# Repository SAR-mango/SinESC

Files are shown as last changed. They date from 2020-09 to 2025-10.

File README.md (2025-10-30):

# Current State of the Project
This project will be revived when I graduate from UCSB. The following changes are planned:

- Switch to HDI PCB
- Switch to discrete half-bridge gate drivers
- Switch to a variant of the STM32G4 MCU (or whatever seems most appropriate)
- Switch to modern MOSFETs with low gate charge, unchanged 40V Vds, similar Rdson, and high avalanche energy rating
- Simplify current sensing topology
- Implement my own FOC algorithm

These changes mostly improve simplicity and robustness, and will make it easier to develop a 4-in-1 version of SinESC after the single version is fully complete. Currently, SinESC successfully spins motors with 90% efficiency, but there are reliability concerns with the TMC6100 gate driver. Also, some software work is required to add DSHOT support. Finally, a more long-term goal is to develop a self-tuning application integrated with Betaflight that can be run to optimize SinESC for a specific motor.

# Overview
SinESC (pronounced "sign ESC," namesake being the sine wave) is an electronic speed controller (ESC) that supports full sinusoidal control of three-phase brushless DC motors used by RC drone pilots. For a brief visual overview of the project and the underlying theory, see [this presentation](https://github.com/SAR-mango/SinESC/blob/master/sinesc_slides/sinesc_slides.pdf) – adapted from a presentation I gave at SpaceX for an onsite interview.

The real-life dimensions of the PCBs pictured below are 15x30mm.
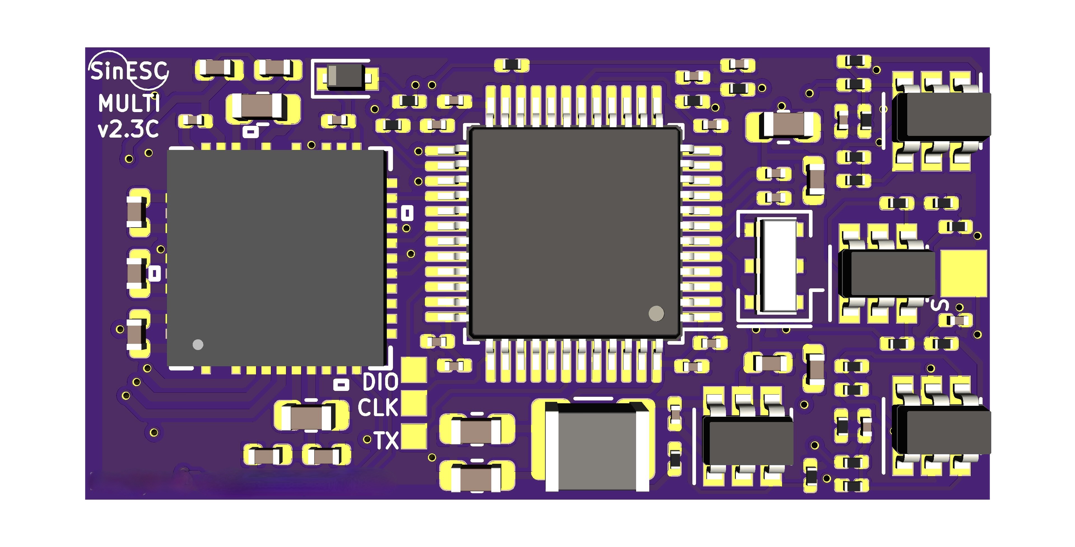
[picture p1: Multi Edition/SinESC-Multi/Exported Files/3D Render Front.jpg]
Multi Edition v2.3C Top

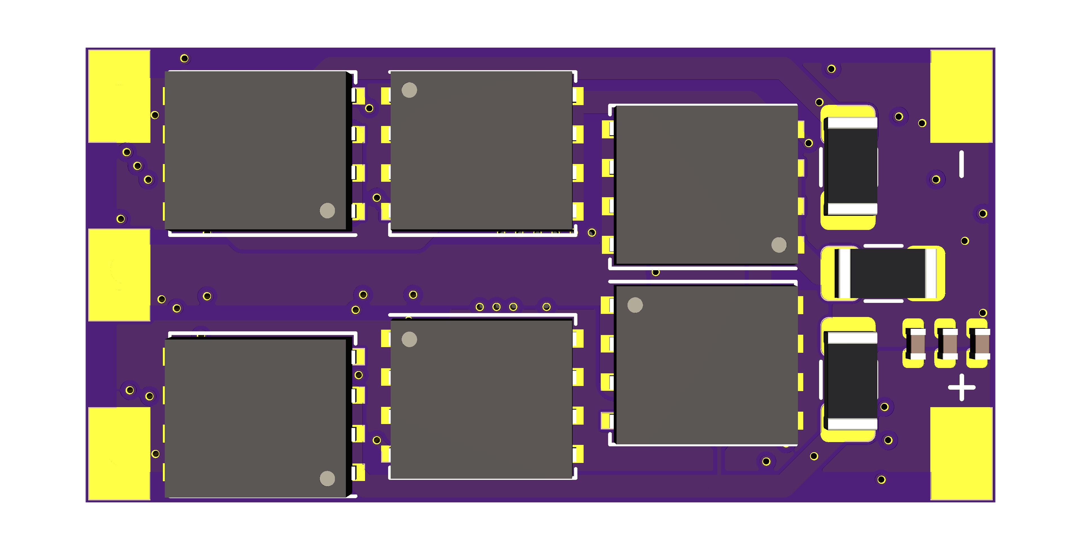
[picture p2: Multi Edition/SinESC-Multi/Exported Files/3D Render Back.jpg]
Multi Edition v2.3C Bottom


# Features, Specifications*
- 90% efficiency (up to 40% longer flight)
- Smooth flight
- Quiet operation
- Bus voltage monitoring for power measurement and under-voltage protection
- Broken-out and labeled debug pins for hackers
- 3–6S Li-po battery support
- Maximum 30A continuous, 40A burst current draw
  - With the greatly-increased efficiency of SinESC, peak motor currents will be significantly lower than before (at a given throttle/thrust level). This does NOT mean your motors produce less power—they are just more efficient.
  - Over-current protection takes advantage of comparators embedded in the microcontroller and triggers immediately at 55A.

\*Several of the above specifications are currently only theoretical; they have not been confirmed with measurements. This page will be updated immediately when any specification changes or is confirmed.

# Sinusoidal Control: Benefits and a Brief Description
Brushless DC motors work best when their phase voltage waveforms are sinusoid-shaped. Try it yourself—connect a BLDC motor to an oscilloscope and spin the rotor with your fingers. You will see a sine wave. 

Regular BLHELI_32 ESCs use a simple "six-point" motor control method in which the phases are energized to bring the rotor to one of six points on a circle. This method is easy to implement as the rotor position at each point will result in a zero-crossing in the back-EMF from the non-energized phase(s), which is easy to detect. This means that the phase voltage waveforms are trapezoid-shaped rather than sinusoid-shaped. This is not ideal as the fields are not *always* aligned with the rotor to maximize torque. This causes the rotor to effectively "jolt in a circle" rather than spin continuously, resulting in lower efficiency and rougher flight. Furthermore, the sharp edges of the trapezoidal signal also introduce high-frequency noise which contributes to the above disadvantages as well. This also makes the motors run louder and hotter.

Sinusoidal control minimizes torque ripple, maximizing efficiency. The magnetic fields are precisely aligned to exert maximum torque on the rotor at *any* given position and power. Minimized torque ripple leads to smoother flight. Greater efficiency (SinESC achieves > 90% efficiency; trapezoidal ESCs typically achieve around 70%) allows for longer flight times and lower peak currents, which can increase battery longevity as well.

# Current-Sense Topology
Not just any ESC can perform sinusoidal control, and not all sinusoidal ESCs are created equal. Sinusoidal control requires that the ESC know the exact position of the rotor in order to properly align the magnetic field. Perfect alignment results in a perfect sine wave.

There are a few ways to find the position of the rotor:
- The first, most obvious method is to put a hall-effect (or similar) sensor on the motor to determine exactly where the rotor is. This sensor simply feeds data to the ESC. However, this is impractical for drones and wings due to durability, size, and weight concerns.
- The second way is to calculate the position of the rotor based on the currents flowing through each phase. Technically, measuring just the total motor current is sufficient, but this leads to poor position estimation and thus reduced performance. Alternatively, each half-bridge can connect to ground through a series current shunt and the voltage drop across each shunt can be amplified and read by an ADC in a microcontroller. This allows for the current through each phase to be known, resulting in far superior performance. Though more complicated, this is the current-sensing topology that SinESC employs.
- Finally, inline current-sensing is also possible. This technique involves placing shunts in series with only two of the three motor phases, since the third phase current can be calculated with Kirchoff's Current Law. However, this requires complicated, expensive amplifiers as high common-mode rejection ratio is critical. Some gate driver ICs integrate these amplifiers, but their gain and offset cannot be tuned to take full advantage of the ADC resolution. At high currents, ADC resolution is very valuable and should not be wasted. Thus, the second method was selected.

# Hardware Achievements
The 15x30mm SinESC Multi Edition PCB uses 0201-sized components when possible for reduced parasitic influences and reduced size. Maximum component density is approximately 50 components/cm². The microcontroller, gate driver, and current-sense amplifiers (all the control electronics) are implemented on the top layer, leaving the bottom layer for the power electronics. This provides room for wide traces. Multi Edition is designed in KiCAD and adheres to OSHPark design rules. All additional libraries are within the project files.

SinESC is designed specifically for efficiency and robustness:
- ST Microelectronics STM32F303C(Bx/Cx) microcontroller
- Maxim Integrated MAX4239 precision op-amps for current-sensing. Incredibly low input offset voltage of 0.1µV. Gain = 30V/V; offset tuned to use the full ADC resolution.
- Low-resistance current shunts (1mΩ) for reduced power loss
- Switching regulator provides logic-level voltage supply for control electronics (efficiency > 80%)
- Thermally optimized PCB layout
- Trinamic Motion Control TMC6100-LA gate driver
  - Fast switching slopes achieved with high gate drive current of 1.5A, decreasing switching losses
- Infineon Technologies BSC010N04LSI N-channel MOSFETs
  - Extremely low on-resistance (Rdson = 1.05mΩ) for reduced power loss
  - High drain-source voltage (Vds = 40V) for immunity to voltage spikes even at 6S Li-po voltages
- High-quality passive components
  - TDK ceramic capacitors
  - Panasonic metal film resistors (all 1% tolerance including shunts)

\*Many of these specifications will change; see the top of this page

# Versions
Regular Semantic Versioning is used for all software components of the project. As for PCB designs, Semantic Versioning has been modified. After Multi v2.3C, versions only reflect the PCB design since schematic changes directly influence the PCB. They are written like so:

vX.YZ where X and Y are numbers and Z is a letter. "v" is sometimes omitted.
- If a minor change is made that does NOT require a new stencil OR an updated BOM, Z is incremented.
- If a minor change requires a new stencil and/or an updated BOM, Y is incremented and Z is reset. Ideally, few minor changes are made between major releases.
- If a major change is made, X is incremented and Y and Z are reset.

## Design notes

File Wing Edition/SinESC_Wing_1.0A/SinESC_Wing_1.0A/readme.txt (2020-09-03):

/**
  * @page Speed regulation using external potentiometer
  * 
  * @verbatim
  ******************** (C) COPYRIGHT 2019 STMicroelectronics *******************
  * @file    STEVAL-ESC001V1\Demonstration\ElectronicSpeedControl\ElectronicSpeedControl.stmcx
  * @author  Motor Control SDK Team
  * @brief   STM32F303 Electronic Speed Control board with BullRunning motor example.
  ******************************************************************************
  * This notice applies to any and all portions of this file
  * that are not between comment pairs USER CODE BEGIN and
  * USER CODE END. Other portions of this file, whether 
  * inserted by the user or by software development tools
  * are owned by their respective copyright owners.
  *
  * Copyright (c) 2019 STMicroelectronics International N.V. 
  * All rights reserved.
  *
  * Redistribution and use in source and binary forms, with or without 
  * modification, are permitted, provided that the following conditions are met:
  *
  * 1. Redistribution of source code must retain the above copyright notice, 
  *    this list of conditions and the following disclaimer.
  * 2. Redistributions in binary form must reproduce the above copyright notice,
  *    this list of conditions and the following disclaimer in the documentation
  *    and/or other materials provided with the distribution.
  * 3. Neither the name of STMicroelectronics nor the names of other 
  *    contributors to this software may be used to endorse or promote products 
  *    derived from this software without specific written permission.
  * 4. This software, including modifications and/or derivative works of this 
  *    software, must execute solely and exclusively on microcontroller or
  *    microprocessor devices manufactured by or for STMicroelectronics.
  * 5. Redistribution and use of this software other than as permitted under 
  *    this license is void and will automatically terminate your rights under 
  *    this license. 
  *
  * THIS SOFTWARE IS PROVIDED BY STMICROELECTRONICS AND CONTRIBUTORS "AS IS" 
  * AND ANY EXPRESS, IMPLIED OR STATUTORY WARRANTIES, INCLUDING, BUT NOT 
  * LIMITED TO, THE IMPLIED WARRANTIES OF MERCHANTABILITY, FITNESS FOR A 
  * PARTICULAR PURPOSE AND NON-INFRINGEMENT OF THIRD PARTY INTELLECTUAL PROPERTY
  * RIGHTS ARE DISCLAIMED TO THE FULLEST EXTENT PERMITTED BY LAW. IN NO EVENT 
  * SHALL STMICROELECTRONICS OR CONTRIBUTORS BE LIABLE FOR ANY DIRECT, INDIRECT,
  * INCIDENTAL, SPECIAL, EXEMPLARY, OR CONSEQUENTIAL DAMAGES (INCLUDING, BUT NOT
  * LIMITED TO, PROCUREMENT OF SUBSTITUTE GOODS OR SERVICES; LOSS OF USE, DATA, 
  * OR PROFITS; OR BUSINESS INTERRUPTION) HOWEVER CAUSED AND ON ANY THEORY OF 
  * LIABILITY, WHETHER IN CONTRACT, STRICT LIABILITY, OR TORT (INCLUDING 
  * NEGLIGENCE OR OTHERWISE) ARISING IN ANY WAY OUT OF THE USE OF THIS SOFTWARE,
  * EVEN IF ADVISED OF THE POSSIBILITY OF SUCH DAMAGE.
  *
  ******************************************************************************
  * @endverbatim
  *
  * @par Demonstration description 
  * 
  *  This demonstration presents motor control application running on 
  * an STEVAL-ESC001V1 electronic speed control board with a BullRunning Motor. 
  *
  * The application features a PWM input for speed reference setting.
  *
  * @par Directory contents 
  * 
  * STEVAL-ESC001V1/Demonstration/ElectronicSpeedControl/readme.txt
  * STEVAL-ESC001V1/Demonstration/ElectronicSpeedControl/ElectronicSpeedControl.ioc
  * STEVAL-ESC001V1/Demonstration/ElectronicSpeedControl/ElectronicSpeedControl.stmcx
  * STEVAL-ESC001V1/Demonstration/ElectronicSpeedControl/Src/esc.c
  * STEVAL-ESC001V1/Demonstration/ElectronicSpeedControl/Src/main.c
  * STEVAL-ESC001V1/Demonstration/ElectronicSpeedControl/Src/mc_config.c
  * STEVAL-ESC001V1/Demonstration/ElectronicSpeedControl/Src/mc_parameters.c
  * STEVAL-ESC001V1/Demonstration/ElectronicSpeedControl/Inc/esc.h
  * STEVAL-ESC001V1/Demonstration/ElectronicSpeedControl/Inc/mc_config.h
  * STEVAL-ESC001V1/Demonstration/ElectronicSpeedControl/Inc/mc_parameters.h
  * STEVAL-ESC001V1/Demonstration/ElectronicSpeedControl/Inc/parameters_conversion_f30x.h
  *
  * @par Hardware and Software environment 
  * 
  * This demonstration runs on the following Hardware Setup:
  * [STEVAL-ESC001V1] + [BullRunning BR2804-1700Kv-1] 
  *
  * The following software tools are needed to run the application:
  *
  * - ST Motor Control SDK, version 5.4.0 or later
  * - STM32CubeMx, version 5.2.0 or later
  * - STM32Cube FW Package for STM32F3 Series, version 1.10.0 or later
  * - IAR EWARM or Keil uVision 5.
  *
  * Note that the current version of this example does not work with STM32CubeIDE 1.0.0.
  *
  * @par How to build it ? 
  * 
  * In order to build the demonstration program, the following is to be done:
  *
  * 1. Open the ElectronicSpeedControl.stmcx file with the STM32 Motor Control Workbench PC software 
  *    tool and save it to another, empty, location.
  *    BEWARE: Do not change the name of the ElectronicSpeedControl.stmcx file, otherwise the example 
  *    will not work properly;
  * 2. Click the Tool -> Generation menu item. This opens a dialog window that lets the users choose
  *    various parameters. Select version 5.2.0 or later for STM32CubeMx, IAR EWARM or Keil MDK Arm 
  *    for the Target toolchain and STM32 FW V1.10.0 or later for the Firmware Package version. Make 
  *    sure to check the HAL - Hardware Abstraction Layer box for the Drive Type. Then, click on the
  *    UPDATE button.
  * 3. Open the generated project with the target IDE;
  * 4. Build the project and load the resulting binary image into your MCU board;
  * 5. Reset your MCU board;
  * 6. Run the example. 
  * 
  * ******************** (C) COPYRIGHT 2019 STMicroelectronics *******************
  **/

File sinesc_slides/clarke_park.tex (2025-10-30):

\begin{tikzpicture}[scale=0.525, every node/.style={transform shape}, >=Latex]
	% --- knobs ---
	\def\R{2}        % circle radius (cm)
	\def\W{3.2}      % waveform width
	\def\A{0.45}     % waveform amplitude
	\def\wfpadT{2} % padding above top circles
	\def\wfpadB{2} % padding below bottom circles
	
	% --- styles ---
	\tikzset{
		circ/.style = {draw, circle, minimum size=2*\R cm},
		axis/.style = {-Latex},
		vec/.style  = {-Latex},
		lbl/.style  = {font=\small}
	}
	
	% --- layout anchors ---
	\coordinate (T1) at (0,5.5);
	\coordinate (T2) at (6.6,5.5);
	\coordinate (T3) at (13.2,5.5);
	\coordinate (B1) at (0,0);
	\coordinate (B2) at (6.6,0);
	\coordinate (B3) at (13.2,0);
	
	% ================== TOP ROW — VOLTAGE ==================
	\node[circ] (C_T1) at (T1) {};
	\draw[axis] (C_T1.center) -- ++(0,\R) node[lbl,above] {$U_D$};
	\draw[axis] (C_T1.center) -- ++(\R,0) node[lbl,right] {$U_Q$};
	\node[align=center, lbl, above=10pt of C_T1] {Rotational steady-state \\ output currents};
	
	\node[circ] (C_T2) at (T2) {};
	\draw[axis] (C_T2.center) -- ++(0,\R) node[lbl,above] {$U_\beta$};
	\draw[axis] (C_T2.center) -- ++(\R,0) node[lbl,right] {$U_\alpha$};
	\node[align=center, lbl, above=10pt of C_T2] {Orthogonal output currents};
	
	\node[circ] (C_T3) at (T3) {};
	\foreach \ang/\name/\pos in {90/U_V/above, -30/U_U/right, -150/U_W/left}{
		\draw[vec] (C_T3.center) -- ++(\ang:\R);
		\node[lbl,\pos] at ($(C_T3.center)+(\ang:\R)$) {$\name$};
	}
	\node[align=center, lbl, above=10pt of C_T3] {Three-phase output waveform};
	
	% arrows across the top row
	\draw[-Latex] ($(C_T1.east)+(0.6,0)$) -- node[above=6pt,lbl]{iPARK}    ($(C_T2.west)+(-0.6,0)$);
	\draw[-Latex] ($(C_T2.east)+(0.6,0)$) -- node[above=6pt,lbl]{iCLARKE} ($(C_T3.west)+(-0.6,0)$);
	\draw[-Latex] ($(C_T3.east)+(0.6,0)$) -- node[above=6pt,lbl]{SVPWM} ($(C_T3.east)+(0.6,0)+(C_T3.west)+(-0.6,0)-(C_T2.east)-(0.6,0)$);
	
	% ================== BOTTOM ROW — CURRENT ==================
	\node[circ] (C_B1) at (B1) {};
	\draw[axis] (C_B1.center) -- ++(0,\R) node[lbl,above] {$I_D$};
	\draw[axis] (C_B1.center) -- ++(\R,0) node[lbl,right] {$I_Q$};
	\node[align=center, lbl, below=6pt of C_B1] {Rotational steady-state \\ direct and quadrature currents};
	
	\node[circ] (C_B2) at (B2) {};
	\draw[axis] (C_B2.center) -- ++(0,\R) node[lbl,above] {$I_\beta$};
	\draw[axis] (C_B2.center) -- ++(\R,0) node[lbl,right] {$I_\alpha$};
	\node[align=center, lbl, below=6pt of C_B2] {Two orthogonal currents};
	
	\node[circ] (C_B3) at (B3) {};
	\foreach \ang/\name/\pos in {90/I_V/above, -30/I_U/right, -150/I_W/left}{
		\draw[vec] (C_B3.center) -- ++(\ang:\R);
		\node[lbl,\pos] at ($(C_B3.center)+(\ang:\R)$) {$\name$};
	}
	\node[align=center, lbl, below=6pt of C_B3] {Three linearly dependent currents};
	
	% arrows across the bottom row
	\draw[-Latex] ($(C_B3.west)+(-0.6,0)$) -- node[above=6pt,lbl]{CLARKE} ($(C_B2.east)+(0.6,0)$);
	\draw[-Latex] ($(C_B2.west)+(-0.6,0)$) -- node[above=6pt,lbl]{PARK}  ($(C_B1.east)+(0.6,0)$);
	\draw[-Latex] ($(C_B1.east)!0.5!(C_B2.west)-(0,1.2)$) node[below=6pt,lbl]{Rotor position $\theta$} -- ($(C_B1.east)!0.5!(C_B2.west)$);
	
	% PID controllers arrow (downward)
	\draw[Latex-]
	($(C_T1.south)+(0,-0.1)$) -- node[lbl,left=3pt,align=center]{PID controller\\$I_{D}=0$\\$I_{Q}\propto\text{torque setpoint}$}
	($(C_B1.north)+(0,0.4)$);
	
	% ================== WAVEFORMS ==================
	% ---- TOP: above circles ----
	\begin{scope}[shift={($(C_T1.center)+(0,\R+\wfpadT)$)}]
		\draw [Red] ({-0.5*\W},0) -- ({0.5*\W},0)
		node[Red,lbl,anchor=west] {$U_Q$};
		\draw [blue] ({-0.5*\W},-\A) -- ({0.5*\W},-\A)
		node[blue,lbl,anchor=west] {$U_D$};
	\end{scope}
	
	\begin{scope}[shift={($(C_T2.center)+(0,\R+\wfpadT)$)}]
		\draw[Red,samples=120,domain=0:360,variable=\t,smooth]
		plot ({-0.5*\W + \W*\t/360},{ \A*sin(\t)}) node[Red,lbl,anchor=west] at ({0.5*\W},{0}) {$U_\alpha$};
		\draw[blue,samples=120,domain=0:360,variable=\t,smooth]
		plot ({-0.5*\W + \W*\t/360},{ \A*sin(\t-90)}) node[blue,lbl,anchor=west] at ({0.5*\W},{-\A}) {$U_\beta$};
	\end{scope}
	
	\begin{scope}[shift={($(C_T3.center)+(0,\R+\wfpadT)$)}]
		\draw[Red,samples=120,domain=0:360,variable=\t,smooth]
		plot ({-0.5*\W + \W*\t/360},{ \A*sin(\t)}) node[Red,lbl,anchor=west] at ({0.5*\W},{0}) {$U_U$};
		\draw[Green,samples=120,domain=0:360,variable=\t,smooth]
		plot ({-0.5*\W + \W*\t/360},{ \A*sin(\t-120)}) node[Green,lbl,anchor=west] at ({0.5*\W},{-\A}) {$U_V$};
		\draw[blue,samples=120,domain=0:360,variable=\t,smooth]
		plot ({-0.5*\W + \W*\t/360},{ \A*sin(\t+120)}) node[blue,lbl,anchor=west] at ({0.5*\W},{\A}) {$U_W$};
	\end{scope}
	
	% ---- BOTTOM: below circles ----
	\begin{scope}[shift={($(C_B1.center)+(0,-\R-\wfpadB)$)}]
		\draw [Red] ({-0.5*\W},0) -- ({0.5*\W},0)
		node[Red,lbl,anchor=west] {$I_Q$};
		\draw [blue] ({-0.5*\W},-\A) -- ({0.5*\W},-\A)
		node[Blue,lbl,anchor=west] {$I_D$};
	\end{scope}
	
	\begin{scope}[shift={($(C_B2.center)+(0,-\R-\wfpadB)$)}]
		\draw[Red,samples=120,domain=0:360,variable=\t,smooth]
		plot ({-0.5*\W + \W*\t/360},{ \A*sin(\t)}) node[Red,lbl,anchor=west] at ({0.5*\W},{0}) {$I_\alpha$};
		\draw[blue,samples=120,domain=0:360,variable=\t,smooth]
		plot ({-0.5*\W + \W*\t/360},{ \A*sin(\t-90)});
		\node[blue,lbl,anchor=west] at ({0.5*\W},{-\A}) {$I_\beta$};
	\end{scope}
	
	\begin{scope}[shift={($(C_B3.center)+(0,-\R-\wfpadB)$)}]
		\draw[Red,samples=120,domain=0:360,variable=\t,smooth]
		plot ({-0.5*\W + \W*\t/360},{ \A*sin(\t)}) node[Red,lbl,anchor=west] at ({0.5*\W},{0}) {$I_U$};
		\draw[Green,samples=120,domain=0:360,variable=\t,smooth]
		plot ({-0.5*\W + \W*\t/360},{ \A*sin(\t-120)}) node[Green,lbl,anchor=west] at ({0.5*\W},{-\A}) {$I_V$};
		\draw[blue,samples=120,domain=0:360,variable=\t,smooth]
		plot ({-0.5*\W + \W*\t/360},{ \A*sin(\t+120)});
		\node[blue,lbl,anchor=west] at ({0.5*\W},{\A}) {$I_W$};
	\end{scope}
\end{tikzpicture}

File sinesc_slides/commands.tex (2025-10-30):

\let\union\cup
\let\intersect\cap
\let\w\omega
\let\e\epsilon
\let\ve\varepsilon
\let\prefto\succ
\let\nprefto\prec
\let\ans\tcboxmath

\let\Re\relax
\DeclareMathOperator{\Re}{Re}
\let\Im\relax
\DeclareMathOperator{\Im}{Im}
\DeclareMathOperator{\Nul}{Nul}
\DeclareMathOperator{\Col}{Col}
\DeclareMathOperator{\Row}{Row}
\DeclareMathOperator{\Span}{Span}
\DeclareMathOperator{\tr}{tr}
\DeclareMathOperator{\rref}{rref}

\newcommand{\V}[1]{V_{\text{#1}}}
\newcommand{\VR}[1]{V_{R_{\text{#1}}}}
\newcommand{\VL}[1]{V_{L_{\text{#1}}}}
\newcommand{\VC}[1]{V_{C_{\text{#1}}}}
\newcommand{\Vv}[1]{v_{\text{#1}}}

\newcommand{\I}[1]{I_{\text{#1}}}
\newcommand{\IR}[1]{I_{R_{\text{#1}}}}
\newcommand{\IL}[1]{I_{L_{\text{#1}}}}
\newcommand{\IC}[1]{I_{C_{\text{#1}}}}
\newcommand{\Ii}[1]{i_{\text{#1}}}

\renewcommand{\P}[1]{P_{\text{#1}}}
\newcommand{\PR}[1]{P_{R_{\text{#1}}}}
\newcommand{\PL}[1]{P_{L_{\text{#1}}}}
\newcommand{\PC}[1]{P_{C_{\text{#1}}}}

\newcommand{\U}[1]{U_{\text{#1}}}
\newcommand{\E}[1]{E_{\text{#1}}}

\newcommand{\A}[1]{A_{\text{#1}}}

\newcommand{\Z}[1]{Z_{\text{#1}}}
\newcommand{\R}[1]{R_{\text{#1}}}
\newcommand{\Rr}[1]{r_{\text{#1}}}
\newcommand{\C}[1]{C_{\text{#1}}}
\newcommand{\Ll}[1]{L_{\text{#1}}}

\newcommand{\qv}[1]{\qty{#1}{\volt}}
\newcommand{\qkv}[1]{\qty{#1}{\kilo\volt}}
\newcommand{\qmv}[1]{\qty{#1}{\milli\volt}}
\newcommand{\quv}[1]{\qty{#1}{\micro\volt}}
\newcommand{\qnv}[1]{\qty{#1}{\nano\volt}}
\newcommand{\qMv}[1]{\qty{#1}{\mega\volt}}

\newcommand{\qa}[1]{\qty{#1}{\ampere}}
\newcommand{\qma}[1]{\qty{#1}{\milli\ampere}}
\newcommand{\qua}[1]{\qty{#1}{\micro\ampere}}
\newcommand{\qna}[1]{\qty{#1}{\nano\ampere}}

\newcommand{\qw}[1]{\qty{#1}{\watt}}
\newcommand{\qkw}[1]{\qty{#1}{\kilo\watt}}
\newcommand{\qmw}[1]{\qty{#1}{\milli\watt}}
\newcommand{\quw}[1]{\qty{#1}{\micro\watt}}
\newcommand{\qnw}[1]{\qty{#1}{\nano\watt}}
\newcommand{\qMw}[1]{\qty{#1}{\mega\watt}}

\newcommand{\qj}[1]{\qty{#1}{\joule}}
\newcommand{\qkj}[1]{\qty{#1}{\kilo\joule}}
\newcommand{\qmj}[1]{\qty{#1}{\milli\joule}}
\newcommand{\quj}[1]{\qty{#1}{\micro\joule}}
\newcommand{\qnj}[1]{\qty{#1}{\nano\joule}}
\newcommand{\qMj}[1]{\qty{#1}{\mega\joule}}

\newcommand{\qr}[1]{\qty{#1}{\ohm}}
\newcommand{\qkr}[1]{\qty{#1}{\kilo\ohm}}
\newcommand{\qmr}[1]{\qty{#1}{\milli\ohm}}
\newcommand{\qur}[1]{\qty{#1}{\micro\ohm}}
\newcommand{\qnr}[1]{\qty{#1}{\nano\ohm}}
\newcommand{\qMr}[1]{\qty{#1}{\mega\ohm}}

\newcommand{\qf}[1]{\qty{#1}{\farad}}
\newcommand{\qmf}[1]{\qty{#1}{\milli\farad}}
\newcommand{\quf}[1]{\qty{#1}{\micro\farad}}
\newcommand{\qnf}[1]{\qty{#1}{\nano\farad}}
\newcommand{\qpf}[1]{\qty{#1}{\pico\farad}}

\newcommand{\qh}[1]{\qty{#1}{\henry}}
\newcommand{\qmh}[1]{\qty{#1}{\milli\henry}}
\newcommand{\quh}[1]{\qty{#1}{\micro\henry}}
\newcommand{\qnh}[1]{\qty{#1}{\nano\henry}}

\newcommand{\qhz}[1]{\qty{#1}{\hertz}}
\newcommand{\qkhz}[1]{\qty{#1}{\kilo\hertz}}
\newcommand{\qMhz}[1]{\qty{#1}{\mega\hertz}}
\newcommand{\qGhz}[1]{\qty{#1}{\giga\hertz}}
\newcommand{\qThz}[1]{\qty{#1}{\tera\hertz}}

\newcommand{\qkm}[1]{\qty{#1}{\kilo\meter}}
\newcommand{\qm}[1]{\qty{#1}{\meter}}
\newcommand{\qcm}[1]{\qty{#1}{\centi\meter}}
\newcommand{\qmm}[1]{\qty{#1}{\milli\meter}}
\newcommand{\qum}[1]{\qty{#1}{\micro\meter}}
\newcommand{\qnm}[1]{\qty{#1}{\nano\meter}}
\newcommand{\qpm}[1]{\qty{#1}{\pico\meter}}

\newcommand{\qkg}[1]{\qty{#1}{\kilo\gram}}
\newcommand{\qg}[1]{\qty{#1}{\gram}}
\newcommand{\qmg}[1]{\qty{#1}{\milli\gram}}
\newcommand{\qug}[1]{\qty{#1}{\micro\gram}}

\newcommand{\qs}[1]{\qty{#1}{\second}}
\newcommand{\qms}[1]{\qty{#1}{\milli\second}}
\newcommand{\qus}[1]{\qty{#1}{\micro\second}}
\newcommand{\qns}[1]{\qty{#1}{\nano\second}}
\newcommand{\qps}[1]{\qty{#1}{\pico\second}}

\newcommand{\qnc}[1]{\qty{#1}{\nano\coulomb}}

\newcommand{\qdb}[1]{\qty{#1}{\decibel}}

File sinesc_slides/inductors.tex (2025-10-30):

\begin{circuitikz}
	\coordinate (C) at (0,0);
	\coordinate (M) at (90:2);
	\coordinate (N) at (-30:2);
	\coordinate (P) at (210:2);
	% Inductors with filled center node and open end nodes
	\draw [L,o-*] (M) to (C);
	\draw (C) to[L,-o] (N);
	\draw [L,o-] (P) to (C);
	% Labels
	\node[above]       at (M) {U};
	\node[below right] at (N) {W};
	\node[below left]  at (P) {V};
\end{circuitikz}

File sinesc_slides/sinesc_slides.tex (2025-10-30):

\input{setup}
\input{commands}
\title{FOC Motor Controller for Drones}
\author{Erk Sampat}
\date{October 3, 2025}
\begin{document}
\begin{frame}
	\begin{center}
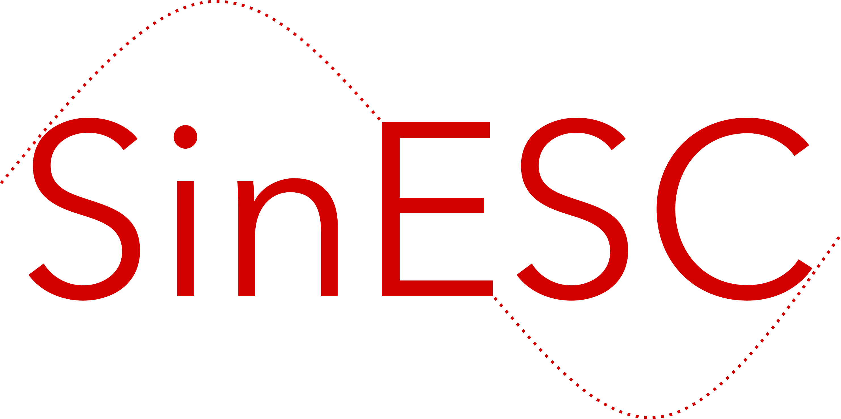
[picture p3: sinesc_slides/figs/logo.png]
		
	\end{center}
	\vskip-0.5in
	\titlepage
\end{frame}
\begin{frame}\frametitle{Outline}
	\begin{enumerate}
		\item Project Introduction
		\item Theory
		\item Design Walkthrough
	\end{enumerate}
\end{frame}
\begin{frame}\frametitle{Project Introduction -- The Problem}
	\begin{itemize}
		\item Typical FPV drone flight time: 5--7 minutes
		\item Off-the-shelf brushless motor controller efficiency $\approx 70\%$
		\item Can we achieve closer to $100\%$?
		\item Yes! With a better control scheme.
		\item Motor controller (``ESC'') is accessible for improvement
	\end{itemize}
	\begin{center}
		
	\end{center}
\end{frame}
\begin{frame}\frametitle{Project Introduction -- System Overview}
	\only<1-2>{
		\begin{center}
			\input{system_diagram}
		\end{center}
	}
	\only<3>{
		\begin{center}
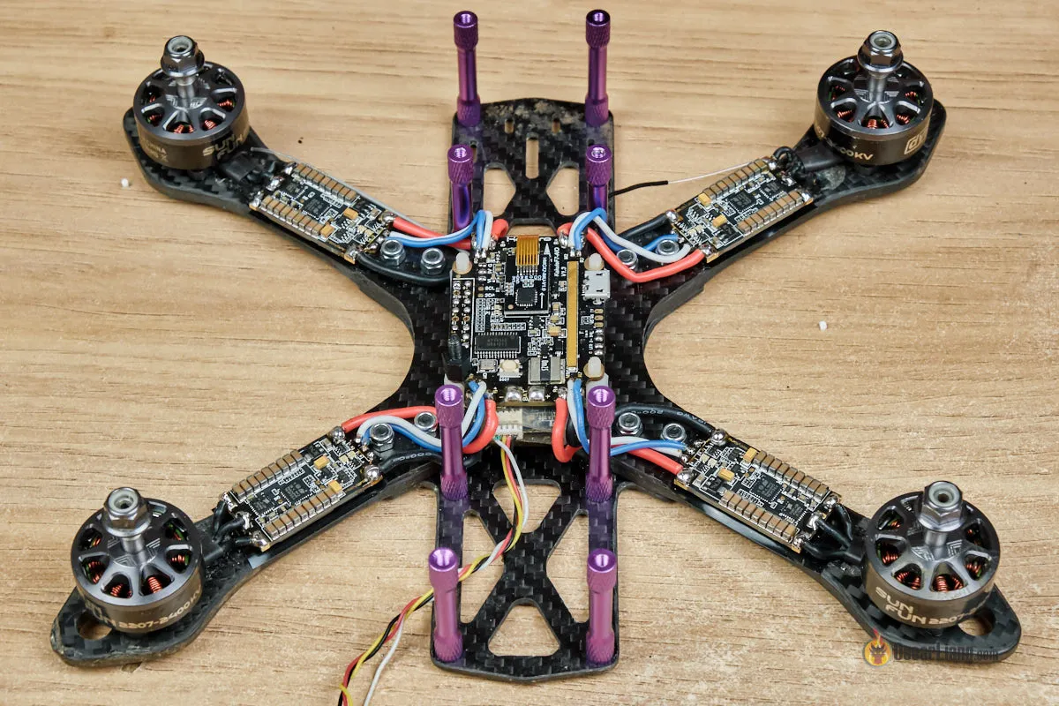
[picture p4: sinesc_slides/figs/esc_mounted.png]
			
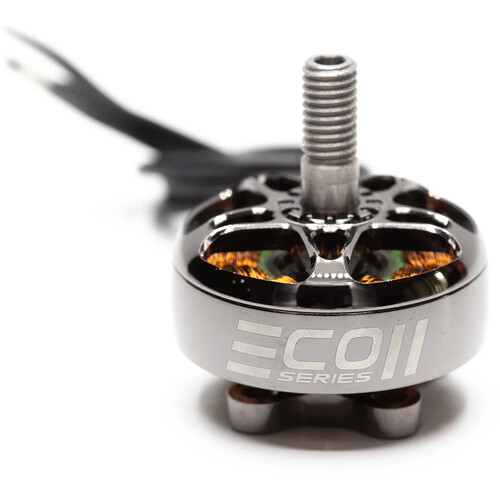
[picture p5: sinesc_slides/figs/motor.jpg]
			
		\end{center}
	}
\end{frame}
\begin{frame}\frametitle{Project Introduction -- Scope}
	\begin{itemize}
		\item Designed/fabricated/tested custom hardware to run sensorless FOC
		\item Hardware initially designed in 2020
		\item Future plan: fully custom firmware
	\end{itemize}
	\begin{center}
		\only<1>{}
		\only<2>{}
	\end{center}
\end{frame}
\begin{frame}\frametitle{Project Introduction -- Primary Specifications}
	\begin{itemize}
		\item $\V{in}$: \qv{12}--\qv{25.2} (4S--6S Li-po battery)
		\item $\I{in}$: \qa{45} continuous, \qa{55} burst (5 seconds)
		\item DSHOT communication protocol support
		\item Size: comparable to off-the-shelf ESC (\qmm{15}$\times$\qmm{30})
		\item Out-of-box compatibility with broad range of motors
		\item High reliability: robustness against\ldots
		\begin{itemize}
			\item Voltage spikes
			\item Rapid throttle (speed command) changes
			\item Physical shock
		\end{itemize}
	\end{itemize}
\end{frame}
\begin{frame}\frametitle{Theory -- Brushless Motors}
	\begin{minipage}{0.5\textwidth}
		\begin{itemize}
			\item Rotor: permanent magnets
			\item Stator: coil windings
			\item Electronically commutated
			\item PMSM: sinusoidal BEMF
			\item BLDC: trapezoidal BEMF\ldots \\
			but often looks sinusoidal due to LC filtering by windings
		\end{itemize}
	\end{minipage}%
	\begin{minipage}{0.5\textwidth}
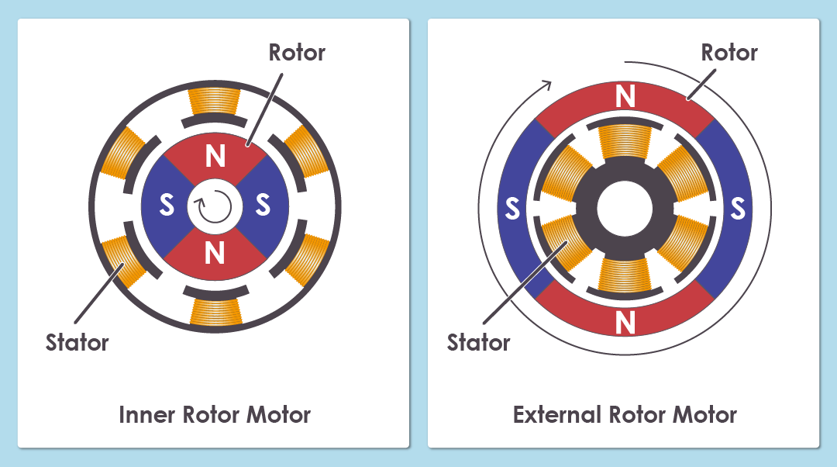
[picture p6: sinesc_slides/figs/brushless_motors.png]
		
		{\scriptsize ablic.com}
		\begin{center}
			\input{inductors}
		\end{center}
	\end{minipage}
\end{frame}
\begin{frame}\frametitle{Theory -- 6-Step Drive}
	\begin{minipage}{0.6\textwidth}
		Operation:
		\begin{itemize}
			\item 6 energized states
			\item Switch upon zero-crossing
			\item PWM controls torque
		\end{itemize}
		Benefits:
		\begin{itemize}
			\item Simple
			\item Low switching loss
			\item Zero-crossings measured on floating phase
		\end{itemize}
		Drawbacks:
		\begin{itemize}
			\item Torque ripple
			\item High-frequency harmonics
			\item Field not always orthogonal to rotor\ldots inefficient
		\end{itemize}
	\end{minipage}%
	\begin{minipage}{0.4\textwidth}
		\begin{center}
			\input{table}
			\input{6_step}
		\end{center}
	\end{minipage}
\end{frame}
\begin{frame}\frametitle{Theory -- Field-Oriented Control}
	\begin{minipage}{0.6\textwidth}
		Operation:
		\begin{itemize}
			\item $\infty$ energized ``states''
			\item Space-vector modulation
			\item PWM controls torque AND field orientation
		\end{itemize}
		Benefits:
		\begin{itemize}
			\item Low torque ripple
			\item Reduced harmonics
			\item Field always orthogonal to rotor\ldots highly efficient
		\end{itemize}
		Drawbacks:
		\begin{itemize}
			\item Complex
			\item Higher switching loss
			\item Difficult to measure BEMF
			\item Requires precise position sensing
		\end{itemize}
	\end{minipage}%
	\begin{minipage}{0.4\textwidth}
		\begin{center}
			\input{table}
			\input{foc}
		\end{center}
	\end{minipage}
\end{frame}
\begin{frame}\frametitle{Theory -- Clarke-Park Transforms}
	\begin{center}
		\input{clarke_park}
	\end{center}
\end{frame}
\begin{frame}\frametitle{Theory -- Sensorless Position Estimation}
	Key point: $\text{knowing BEMF and phase currents}=\text{knowing rotor position}$
	\begin{enumerate}
		\item Measure phase voltage during short non-energized intervals
		\begin{itemize}
			\item High speed required for large BEMF\ldots
			\item but non-energized intervals shorten as speed increases
		\end{itemize}
		\item Estimate BEMF using measured currents and motor parameters $L$ and $R$ per phase
		\item Calculate electrical angle of rotor, differentiate w.r.t. time to obtain speed
		\begin{itemize}
			\item Helps to know rotor inertia
		\end{itemize}
	\end{enumerate}
	More advanced techniques: high-frequency injection, PLL, etc.
\end{frame}
\begin{frame}\frametitle{Design Walkthrough -- Schematic}
	
\end{frame}
\begin{frame}\frametitle{Design Walkthrough -- Key Component Characteristics}
	\begin{minipage}[t]{0.5\textwidth}
		Microcontroller
		\begin{itemize}
			\item ST part -- FOC library
			\item Ample analog peripherals
			\item 32 bit, medium performance
		\end{itemize}
	\end{minipage}%
	\begin{minipage}[t]{0.5\textwidth}
		Current-sense amplifiers
		\begin{itemize}
			\item Low noise
			\item Sufficient bandwidth
			\item Temperature stability
		\end{itemize}
	\end{minipage}
	\vskip 1em
	\begin{minipage}[t]{0.5\textwidth}
		FET driver
		\begin{itemize}
			\item Simplicity
			\item Robustness against transients
			\item Sufficient drive current
			\item High-side N support
		\end{itemize}
	\end{minipage}%
	\begin{minipage}[t]{0.5\textwidth}
		MOSFETs
		\begin{itemize}
			\item $\R{ds,on}$ low enough
			\item $Q_{\text{g}}$ as low as possible
			\item Sufficient $\V{ds}$
			\item N-channel
		\end{itemize}
	\end{minipage}
\end{frame}
\begin{frame}\frametitle{Design Walkthrough -- Component Choices}
	\begin{minipage}[t]{0.5\textwidth}
		Microcontroller: STM32F3xx
		\begin{itemize}
			\item Multiple ADCs
			\item Comparators for OCP
			\item ST FOC library
			\item Cortex-M3
		\end{itemize}
	\end{minipage}%
	\begin{minipage}[t]{0.5\textwidth}
		Current-sense amplifiers: MAX4239
		\begin{itemize}
			\item Somewhat poor choice
			\item \quv{0.1} input offset voltage unnecessary
			\item Too expensive
		\end{itemize}
	\end{minipage}
	\vskip 1em
	\begin{minipage}[t]{0.5\textwidth}
		FET driver: TMC6100
		\begin{itemize}
			\item Expensive and complicated
			\item Charge pump for 100\% duty cycle operation
			\item Controlled through SPI
		\end{itemize}
	\end{minipage}%
	\begin{minipage}[t]{0.5\textwidth}
		MOSFETS: BSC010N04LSI
		\begin{itemize}
			\item $\V{ds}=\qv{40}$
			\item $R_{\text{ds,on}}=\qmr{1.05}$: too low
			\item $Q_{\text{g}}=\qnc{87}$: too high
			\item Ideally, find middle ground by considering product $R_{\text{ds,on}}Q_{\text{g}}$
		\end{itemize}
	\end{minipage}
\end{frame}
\begin{frame}\frametitle{Design Walkthrough -- Challenges}
	\begin{minipage}{0.6\textwidth}
		\begin{itemize}
			\item SPI configuration
			\item Inappropriate current specification
			\item \qv{3.3} rail issue
			\item Gate driver charge pump filter
			\item Form factor; difficulty with testing
			\item ADC resolution for current sensing
		\end{itemize}
	\end{minipage}%
	\begin{minipage}{0.4\textwidth}
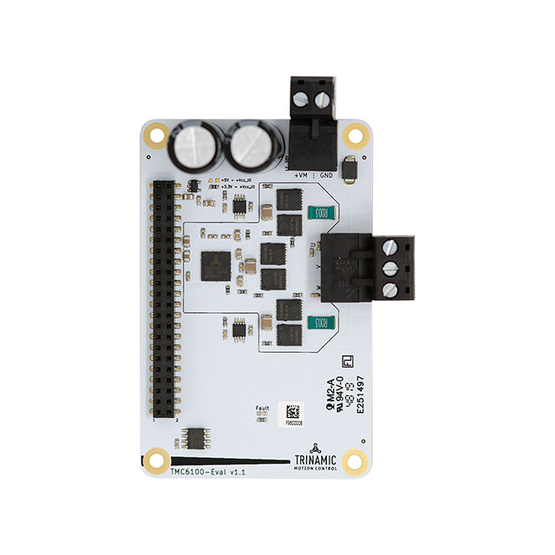
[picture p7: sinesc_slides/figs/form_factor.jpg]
		
	\end{minipage}
	\begin{center}
		
		
	\end{center}
\end{frame}
\begin{frame}\frametitle{Design Walkthrough -- Assembly}
	\begin{itemize}
		\item Initially: stencil, pick \& place, and reflow manually
		\item Later: assembled at PCBWay
	\end{itemize}
	\begin{center}
		
		
	\end{center}
\end{frame}
\end{document}

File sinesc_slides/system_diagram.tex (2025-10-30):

\begin{tikzpicture}[scale=0.9,transform shape]
	% Paths, nodes and wires:
	\node[shape=rectangle, draw, line width=0.5pt, minimum width=5.982cm, minimum height=4.982cm] at (35, -4){};
	\node[shape=rectangle, draw, line width=0.5pt, minimum width=2.232cm, minimum height=0.982cm] at (35, -0.75){} node[anchor=center, align=center, text width=1.862cm, inner sep=5.5pt] at (35, -0.75){Battery};
	\node[shape=rectangle, draw, line width=0.5pt, minimum width=2.232cm, minimum height=0.982cm] at (30.625, -4){} node[anchor=center, align=center, text width=1.862cm, inner sep=5.5pt] at (30.625, -4){RC Receiver};
	\node[shape=rectangle, draw, line width=0.5pt, dash pattern={on 2pt off 1pt}, minimum width=2.482cm, minimum height=0.982cm] at (35, -5.5){} node[anchor=center, align=center, text width=2.112cm, inner sep=5.5pt] at (35, -5.5){IMU};
	\node[shape=rectangle, draw, line width=0.5pt, dash pattern={on 2pt off 1pt}, minimum width=2.482cm, minimum height=0.982cm] at (35, -4){} node[anchor=center, align=center, text width=2.112cm, inner sep=5.5pt] at (35, -4){MCU};
	\node[shape=rectangle, draw, line width=0.5pt, dash pattern={on 2pt off 1pt}, minimum width=2.482cm, minimum height=0.982cm] at (35, -2.5){} node[anchor=center, align=center, text width=2.112cm, inner sep=5.5pt] at (35, -2.5){Power Distribution};
	\path[draw=Red, line width=0.8pt, -latex] (35, -1.25) -- (35, -2);
	\draw[-latex] (31.75, -4) -- (33.75, -4);
	\draw[-latex] (35, -5) -- (35, -4.5);
	\path[draw=Red, line width=0.8pt, -latex] (36.75, -2.5) -- (36.75, -5.5) -- (36.25, -5.5);
	\node[shape=rectangle, minimum width=3.215cm, minimum height=0.965cm] at (33.375, -1.75){} node[anchor=center, align=center, text width=2.827cm, inner sep=6pt] at (33.375, -1.75){Flight Controller};
	\only<1>{\node[shape=rectangle, draw, line width=0.5pt, minimum width=2.215cm, minimum height=0.965cm] at (39.375, -4){} node[anchor=center, align=center, text width=1.827cm, inner sep=6pt] at (39.375, -4){4x ESC};}
	\only<2>{\node[shape=rectangle, draw=blue, line width=1pt, minimum width=2.215cm, minimum height=0.965cm] at (39.375, -4){} node[anchor=center, align=center, text width=1.827cm, inner sep=6pt] at (39.375, -4){4x ESC};}
	\node[shape=rectangle, draw, line width=0.5pt, minimum width=2.232cm, minimum height=0.982cm] at (39.375, -5.5){} node[anchor=center, align=center, text width=1.862cm, inner sep=5.5pt] at (39.375, -5.5){4x Motor};
	\path[draw=Red, line width=0.8pt, -latex] (36.75, -4.25) -- (36.25, -4.25);
	\draw[-latex] (35, -3) -- (35, -3.5);
	\path[draw=Red, line width=0.8pt, latex-] (30.625, -3.5) |- (30.75, -2.5) -- (33.75, -2.5);
	\path[draw=Red, line width=0.8pt, -latex] (36.25, -2.5) -| (39.375, -3.5);
	\draw[-latex] (36.25, -4) -- (38.25, -4);
	\path[draw=Red, line width=0.8pt, -latex] (39.375, -4.5) -- (39.375, -5);
\end{tikzpicture}

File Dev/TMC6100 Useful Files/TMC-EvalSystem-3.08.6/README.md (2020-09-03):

# TMC-EvalSystem

Trinamic Evaluation System

## Setup
To clone this repository, simply use the following command in order to clone submodules recursively:  
`git clone --recurse-submodules git@github.com:trinamic/TMC-EvalSystem.git`

## Changelog

For detailed changelog, see commit history.

### Version 3.06: (Beta)
* Full TMC2160 support
* Landungsbruecke HW v2.0 support with internal HWID detection for future revisions
* Internal/external step/dir generator handling in FW and IDE
* Various bugfixes
* Internal optimizations

### Version 3.05: (Released)
* TMC5072-EVAL Critical bugfix at register access
* TMC2160-EVAL Corrected pin layout

### Version 3.02: (Released)
* Reworked chip register configuration mechanisms (generic reset/restore procedures implemented in API)
* Changed register accesses to use a unified Mask/Shift macro approach
* Various bugfixes

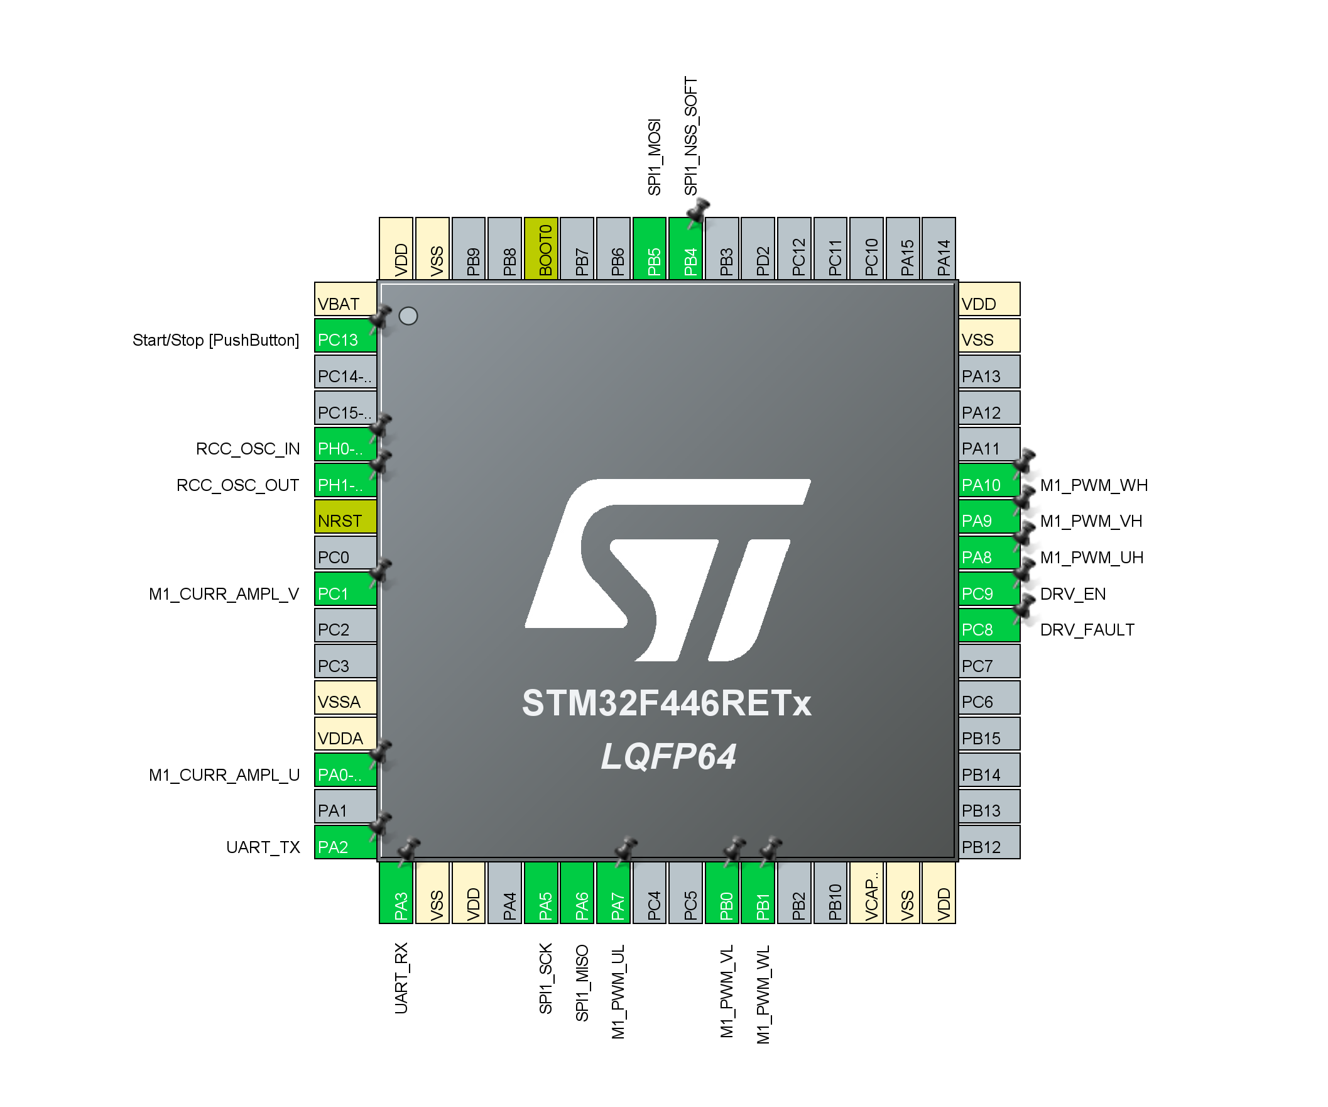
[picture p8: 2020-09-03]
Dev/F446RE_Eval_Test/Pinout.png

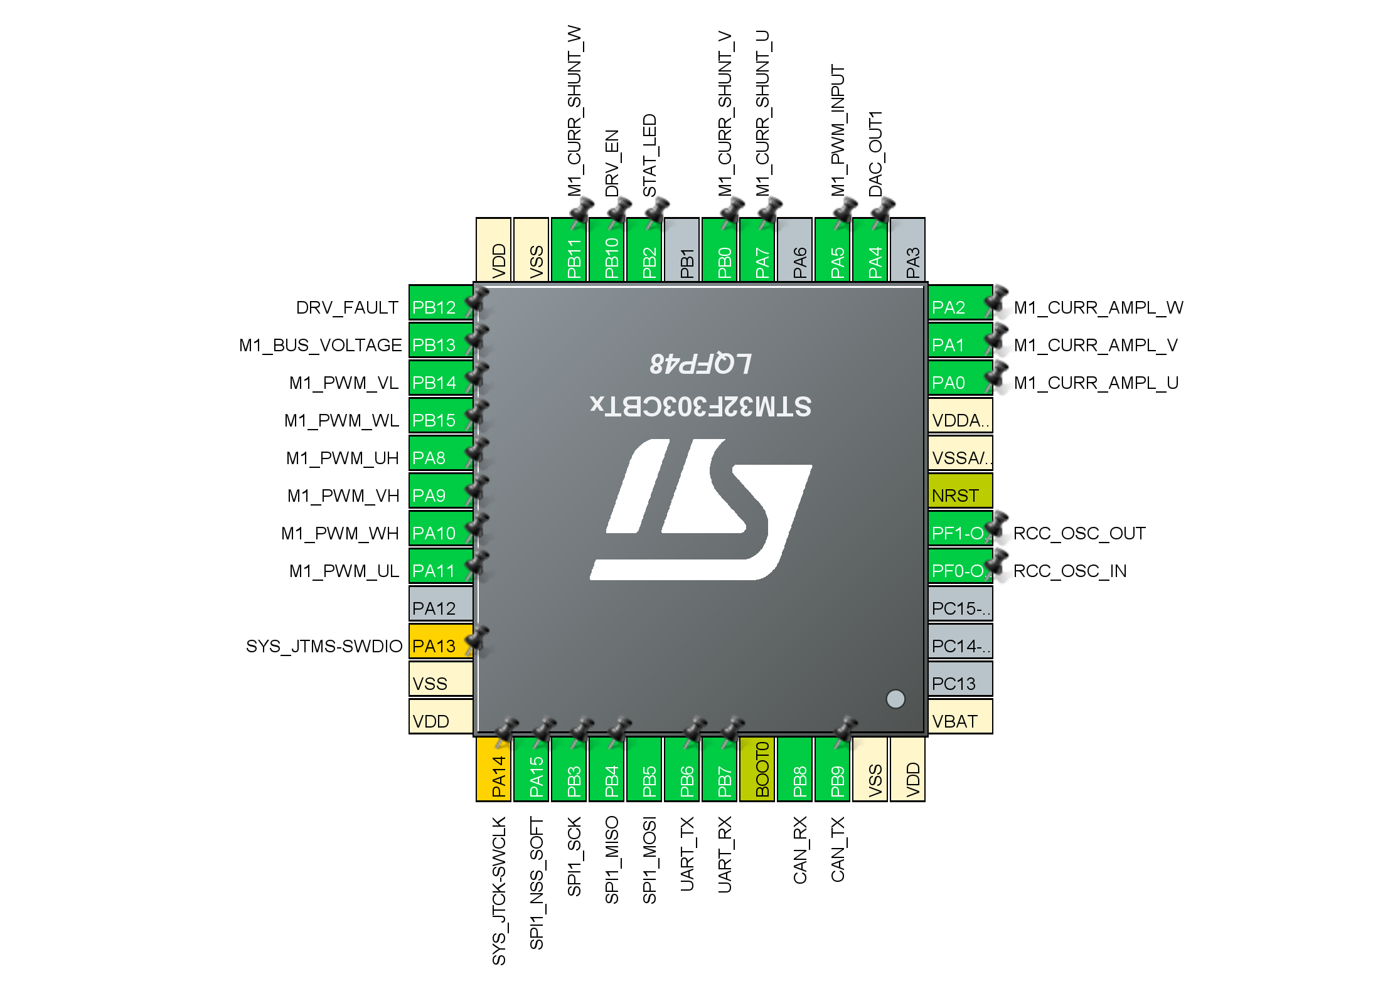
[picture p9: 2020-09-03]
Wing Edition/Pinout.png

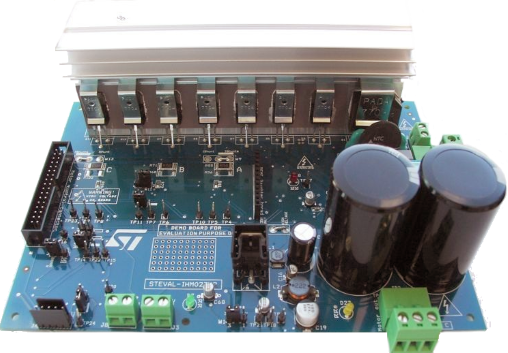
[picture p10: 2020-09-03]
Dev/Original ST Software/STSW-ESC001V1/ESC_STMotorProfiler_addon/resources/assets/images/power/en_steval-ihm023v3.png

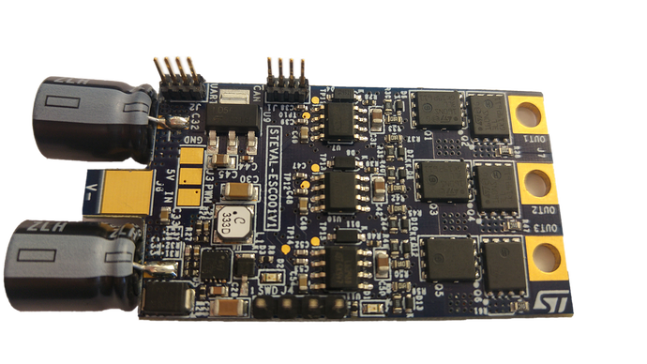
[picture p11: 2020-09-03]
Dev/Original ST Software/STSW-ESC001V1/ESC_STMotorProfiler_addon/resources/assets/boardConfigs/images/STEVAL-ESC001V1_PB.png

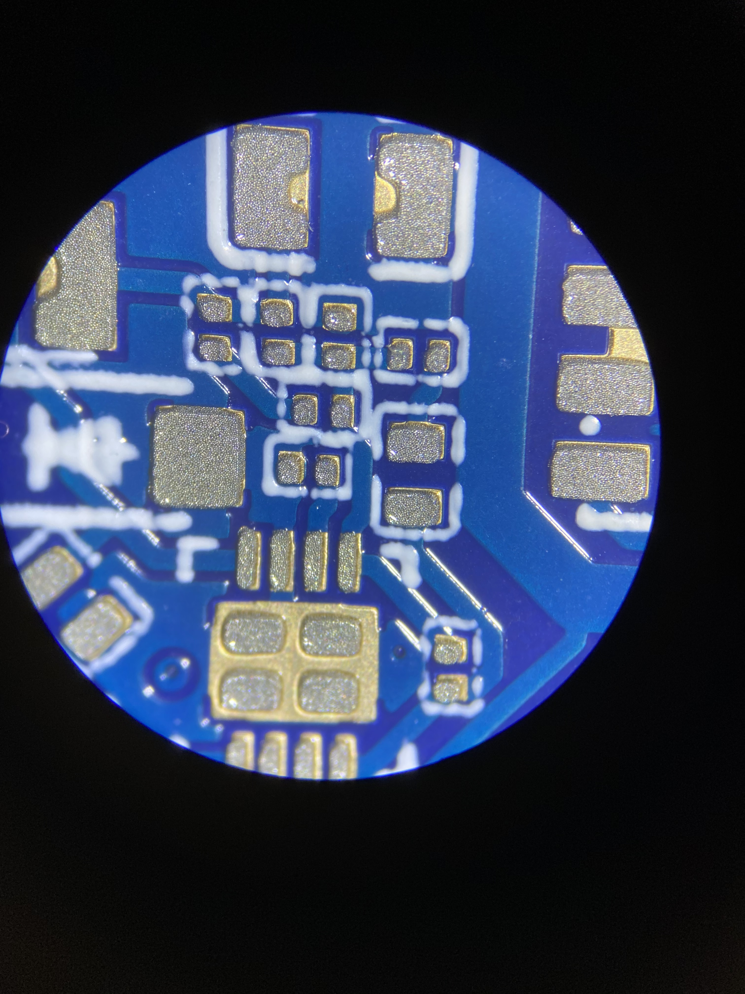
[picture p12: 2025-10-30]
sinesc_slides/figs/stencil_microscope.jpeg

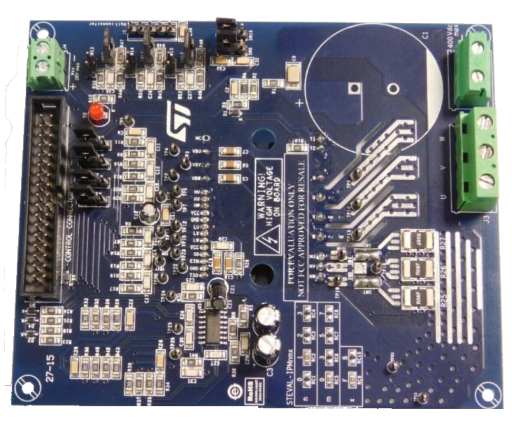
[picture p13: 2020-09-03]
Dev/Original ST Software/STSW-ESC001V1/ESC_STMotorProfiler_addon/resources/assets/images/power/steval-ipm10f.png

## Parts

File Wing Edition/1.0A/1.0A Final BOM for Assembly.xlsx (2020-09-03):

Name | Designator | Footprint | Quantity
8MHz | X1 | - | 1
Red LED | LED1 | LED_0201 | 1
MAX4239AUT+T | U5,U6,U7 | SOT23-6 | 3
SM04B-GHS-TB(LF)(SN)- | J1 | - | 1
BAT30F4 | D1 | D0201 | 1
PMEG4030ER/8X | D2 | SOD-123 | 1
1mΩ | R3,R1,R2 | R1206 | 3
0Ω | R17,R16,R20,R21,R18,R19 | R0201 | 6
680Ω | R28,R24,R34 | R0201 | 3
220Ω | R8 | R0201 | 1
100kΩ | R5 | R0201 | 1
12kΩ | R6 | R0201 | 1
86.6Ω | R10,R25,R31 | R0201 | 3
1.5kΩ | R9 | R0201 | 1
120Ω | R4 | R0201 | 1
249Ω | R11 | R0201 | 1
4.99kΩ | R14 | R0201 | 1
1.1kΩ | R15 | R0201 | 1
220kΩ | R7 | R0201 | 1
976Ω | R13,R27,R33 | R0201 | 3
15kΩ | R22,R29,R35 | R0201 | 3
470Ω | R23,R30,R36 | R0201 | 3
5.1kΩ | R12,R26,R32 | R0201 | 3
6.8nF | C25,C32,C35 | C0201 | 3
100nF | C6,C12,C4,C2,C1,C13,C3 | C0201 | 7
2.2nF | C24 | C0201 | 1
1µF | C10,C28,C29,C30 | C0402 | 4
22µF | C27 | C0805 | 1
10nF | C5 | C0201 | 1
10µF | C14 | C0805 | 1
470nF | C15,C26 | C0402 | 2
4.7µF | C11 | C0603 | 1
1nF | C9,C7,C8 | C0201 | 3
22nF | C19 | C0603 | 1
100nF | C22,C23,C16 | C0402 | 3
15nF | C31,C34,C33 | C0402 | 3
22nF | C20 | C0402 | 1
10µF | C17 | C0603 | 1
2.2µF | C18 | C0402 | 1
470pF | C21 | C0201 | 1
TMC6100-LA | U4 | LQFP37 | 1
TJA1051TK/3,118 | U1 | HVSON-8 | 1
BSC010N04LSI | Q1,Q2,Q3,Q4,Q5,Q6 | PG-TDSON-8-FL | 6
L7981TR | U3 | VFQFPN8 | 1
10µH | L1 | IND-SMD_L2.0-W2.0 | 1
STM32F303CBT7 | U2 | STM-LQFP48 | 1

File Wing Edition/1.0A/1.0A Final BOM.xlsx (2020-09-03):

Index | Quantity | Part Number | Manufacturer Part Number | Description | Customer Reference | Backorder | Unit Price | Extended Price
1 | 1 | SMD4300TF10-ND | SMD4300TF10 | TACK FLUX 10CC WATER WASHABLE |  | 0 | 17.95 | $17.95
2 | 12 | 445-12081-1-ND | CGA1A2X7R1C682K030BA | CAP CER 6800PF 16V X7R 0201 |  | 0 | 0.085 | $1.02
3 | 4 | P122674CT-ND | ERJ-1GNF1101C | RES SMD 1.1K OHM 1% 1/20W 0201 |  | 0 | 0.1 | $0.40
4 | 1 | DS18B20+T&RCT-ND | DS18B20+T&R | SENSOR DIGITAL -55C-125C TO92-3 |  | 0 | 3.92 | $3.92
5 | 4 | P122834CT-ND | ERJ-1GNF2203C | RES SMD 220K OHM 1% 1/20W 0201 |  | 0 | 0.1 | $0.40
6 | 4 | P122864CT-ND | ERJ-1GNF2490C | RES SMD 249 OHM 1% 1/20W 0201 |  | 0 | 0.1 | $0.40
7 | 4 | P122743CT-ND | ERJ-1GNF1501C | RES SMD 1.5K OHM 1% 1/20W 0201 |  | 0 | 0.1 | $0.40
8 | 4 | P123046CT-ND | ERJ-1GNF4991C | RES SMD 4.99K OHM 1% 1/20W 0201 |  | 0 | 0.1 | $0.40
9 | 12 | P123124CT-ND | ERJ-1GNF6800C | RES SMD 680 OHM 1% 1/20W 0201 |  | 0 | 0.049 | $0.59
10 | 4 | P122694CT-ND | ERJ-1GNF1202C | RES SMD 12K OHM 1% 1/20W 0201 |  | 0 | 0.1 | $0.40
11 | 4 | P122655CT-ND | ERJ-1GNF1003C | RES SMD 100K OHM 1% 1/20W 0201 |  | 0 | 0.1 | $0.40
12 | 12 | P123030CT-ND | ERJ-1GNF4700C | RES SMD 470 OHM 1% 1/20W 0201 |  | 0 | 0.049 | $0.59
13 | 12 | P123051CT-ND | ERJ-1GNF5101C | RES SMD 5.1K OHM 1% 1/20W 0201 |  | 0 | 0.049 | $0.59
14 | 12 | P123188CT-ND | ERJ-1GNF86R6C | RES SMD 86.6 OHM 1% 1/20W 0201 |  | 0 | 0.049 | $0.59
15 | 4 | P122831CT-ND | ERJ-1GNF2200C | RES SMD 220 OHM 1% 1/20W 0201 |  | 0 | 0.1 | $0.40
16 | 4 | P122692CT-ND | ERJ-1GNF1200C | RES SMD 120 OHM 1% 1/20W 0201 |  | 0 | 0.1 | $0.40
17 | 12 | P123214CT-ND | ERJ-1GNF9760C | RES SMD 976 OHM 1% 1/20W 0201 |  | 0 | 0.049 | $0.59
18 | 12 | P122744CT-ND | ERJ-1GNF1502C | RES SMD 15K OHM 1% 1/20W 0201 |  | 0 | 0.049 | $0.59
19 | 10 | 490-16354-1-ND | GRM155R61H474KE11D | CAP CER 0.47UF 50V X5R 0402 |  | 0 | 0.13 | $1.30
20 | 24 | 2019-RK73Z1HTTCCT-ND | RK73Z1HTTC | RES 0 OHM JUMPER 0201 |  | 0 | 0.051 | $1.22
21 | 16 | 587-6278-1-ND | UMK105CBJ105MV-F | CAP CER 1UF 50V X5R 0402 |  | 0 | 0.193 | $3.09
22 | 50 | 445-13671-1-ND | C0603X5R1E104K030BB | CAP CER 0.1UF 25V X5R 0201 |  | 0 | 0.045 | $2.25
23 | 12 | 445-7275-1-ND | C0603X7R1E102K030BA | CAP CER 1000PF 25V X7R 0201 |  | 0 | 0.051 | $0.61
24 | 4 | 445-9090-1-ND | C1005X5R1E225K050BC | CAP CER 2.2UF 25V X5R 0402 |  | 0 | 0.32 | $1.28
25 | 12 | 445-12244-1-ND | CGA2B2X7R1E153K050BA | CAP CER 0.015UF 25V X7R 0402 |  | 0 | 0.057 | $0.68
26 | 4 | 445-12113-1-ND | CGA1A2X7R1H471K030BA | CAP CER 470PF 50V X7R 0201 |  | 0 | 0.11 | $0.44
27 | 12 | 490-10458-1-ND | GRM155R62A104KE14D | CAP CER 0.1UF 100V X5R 0402 |  | 0 | 0.031 | $0.37
28 | 4 | 490-10749-1-ND | GRM21BR61E226ME44L | CAP CER 22UF 25V X5R 0805 |  | 0 | 0.52 | $2.08
29 | 4 | 445-7332-1-ND | C1005X7R1H223K050BB | CAP CER 0.022UF 50V X7R 0402 |  | 0 | 0.13 | $0.52
30 | 4 | 587-6028-1-ND | UMK063BJ222KP-F | CAP CER 2200PF 50V X5R 0201 |  | 0 | 0.12 | $0.48
31 | 4 | 445-9050-1-ND | C1608X5R1E475K080AC | CAP CER 4.7UF 25V X5R 0603 |  | 0 | 0.38 | $1.52
32 | 4 | 445-9015-1-ND | C1608X5R1E106M080AC | CAP CER 10UF 25V X5R 0603 |  | 0 | 0.8 | $3.20
33 | 25 | BSC010N04LSIATMA1CT-ND | BSC010N04LSIATMA1 | MOSFET N-CH 40V 37A 8TDSON |  | 0 | 2.3372 | $58.43
34 | 4 | 445-2275-1-ND | C1608X7R2A223K080AA | CAP CER 0.022UF 100V X7R 0603 |  | 0 | 0.11 | $0.44
35 | 10 | 587-5943-1-ND | TMK063B7103KP-F | CAP CER 10000PF 25V X7R 0201 |  | 0 | 0.025 | $0.25
36 | 4 | 497-15253-1-ND | BAT30F4 | DIODE SCHOTTKY 30V 300MA 0201 |  | 0 | 0.37 | $1.48
37 | 12 | MAX4239AUT+TCT-ND | MAX4239AUT+T | IC OPAMP GP 1 CIRCUIT SOT23-6 |  | 0 | 1.823 | $21.88
38 | 4 | 497-10814-1-ND | L7981TR | IC REG BUCK ADJ 3A 8VFQFPN |  | 0 | 1.78 | $7.12
39 | 4 | 490-16631-1-ND | LQH5BPN100M38L | FIXED IND 10UH 2.2A 56 MOHM SMD |  | 0 | 0.7 | $2.80
40 | 4 | 568-8686-1-ND | TJA1051TK/3,118 | IC TRANSCEIVER HALF 1/1 8HVSON |  | 0 | 1.03 | $4.12
41 | 4 | 497-17422-ND | STM32F303CBT7 | IC MCU 32BIT 128KB FLASH 48LQFP |  | 0 | 5.42 | $21.68
42 | 4 | 1727-7643-1-ND | PMEG4030ER/8X | DIODE SCHOTTKY 40V 3A SOD123W |  | 0 | 0.35 | $1.40
43 | 12 | 696-1369-1-ND | CSR1206-0R001F1 | RES 0.001 OHM 1% 1W 1206 |  | 0 | 0.49 | $5.88
44 | 4 | 490-17961-1-ND | CSTNE8M00GH5C000R0 | CERAMIC RES 8.0000MHZ 33PF SMD |  | 0 | 0.36 | $1.44
45 | 4 | 1460-TMC6100-LA-TCT-ND | TMC6100-LA-T | GATE DRIVER IC 8-60V QFN37 |  | 0 | 3.13 | $12.52
46 | 4 | 490-18664-1-ND | GRM21BR61H106ME43L | CAP CER 10UF 50V X5R 0805 |  | 0 | 0.48 | $1.92
47 | 4 | 754-2024-1-ND | APG0603SURC-TT | LED RED CLEAR 2SMD |  | 0 | 0.5 | $2.00
 |  |  |  |  |  |  | Subtotal | $192.43

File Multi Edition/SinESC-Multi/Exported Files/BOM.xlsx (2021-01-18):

SinESC Multi v2.3C—Bill of Materials (BOM) | Line Item | Qty | Reference(s) | Value | Manufacturer Part # | Package/Footprint
Source: SinESC\Multi Edition\SinESC-Multi\SinESC-Multi.sch | 1 | 7 | C1, C2, C4, C8, C20, C23, C30 | 100nF | C0603X5R1E104K030BB | C0201
Generated on: 12/30/2020 | 2 | 10 | C3, C5, C6, C7, C9, C10, C12, C14, C15, C19 | 6.8nF | GRM033R71E682KE14D | C0201
Last Updated: 1/18/2021 | 3 | 12 | C11, C16, C17, C18, C21, C22, C26, C28, C29, C31, C32, C33 | 1µF | UMK105CBJ105MV-F | C0402
Tool: Eeschema (5.1.6)-1 | 4 | 4 | C13, C25, C34, C35 | 10µF | C1608X5R1E106M080AC | C0603
Generator: bom_csv_grouped_by_value.py | 5 | 1 | C24 | 22nF | C1608X7R2A223K080AA | C0603
Total Component Count: 75 | 6 | 1 | C27 | 100nF | C1005X7R1H104K050BB | C0402
Unique Component Count: 23 | 7 | 1 | D1 | BAT30KFILM | BAT30KFILM | SOD-523
BOM Consolidation Ratio (Total:Unique): 3.261:1 | 8 | 1 | L1 | 10µH | CBC3225T100KR | L1210
 | 9 | 6 | Q1, Q2, Q3, Q4, Q5, Q6 | BSC010N04LSI | BSC010N04LSIATMA1 | TDSON-8-1
 | 10 | 3 | R1, R10, R19 | 86.6Ω | ERJ-1GNF86R6C | R0201
 | 11 | 3 | R2, R6, R11 | 1.5kΩ | ERJ-1GNF1501C | R0201
 | 12 | 3 | R3, R7, R12 | 1mΩ | CSR1206-0R001F1 | R1206
 | 13 | 3 | R4, R13, R20 | 5.1kΩ | ERJ-1GNF5101C | R0201
 | 14 | 3 | R5, R14, R21 | 976Ω | ERJ-1GNF9760C | R0201
 | 15 | 4 | R8, R16, R17, R22 | 15kΩ | ERJ-1GNF1502C | R0201
 | 16 | 3 | R9, R18, R23 | 470Ω | ERJ-1GNF4700C | R0201
 | 17 | 2 | R15, R25 | 120kΩ | ERJ-1GNF1203C | R0201
 | 18 | 1 | R24 | 52.3kΩ | ERJ-1GNF5232C | R0201
 | 19 | 1 | U1 | STM32F303CBT7 | STM32F303CBT7 | LQFP48-7x7mm-P0.5mm
 | 20 | 3 | U2, U3, U5 | MAX4239AUT | MAX4239AUT+T | SOT23-6
 | 21 | 1 | U4 | TMC6100-LA | TMC6100-LA-T | QFN37-EP-7x7mm
 | 22 | 1 | U6 | TPS560430XDBVR | TPS560430XDBVR | SOT23-6
 | 23 | 1 | Y1 | 8MHz | CSTNE8M00G550000R0 | Resonator_SMD_muRata_CSTxExxV-3Pin_3.0x1.1mm

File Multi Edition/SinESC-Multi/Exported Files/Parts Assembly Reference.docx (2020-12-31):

SinESC Multi v2.3C Assembly Reference

Line Item | Qty | Reference(s) | Value
1 | 7 | C1, C2, C4, C8, C20, C23, C30 | 100nF
2 | 10 | C3, C5, C6, C7, C9, C10, C12, C14, C15, C19 | 6.8nF
3 | 12 | C11, C16, C17, C18, C21, C22, C26, C28, C29, C31, C32, C33 | 1µF
4 | 4 | C13, C25, C34, C35 | 10µF
5 | 1 | C24 | 22nF
6 | 1 | C27 | 100nF
7 | 1 | D1 | BAT30KFILM
8 | 1 | L1 | 10µH
9 | 6 | Q1, Q2, Q3, Q4, Q5, Q6 | BSC010N04LSI
10 | 3 | R1, R10, R19 | 86.6Ω
11 | 3 | R2, R6, R11 | 1.5kΩ
12 | 3 | R3, R7, R12 | 1mΩ
13 | 3 | R4, R13, R20 | 5.1kΩ
14 | 3 | R5, R14, R21 | 976Ω
15 | 4 | R8, R16, R17, R22 | 15kΩ
16 | 3 | R9, R18, R23 | 470Ω
17 | 2 | R15, R25 | 120kΩ
18 | 1 | R24 | 52.3kΩ
19 | 1 | U1 | STM32F303CBT7
20 | 3 | U2, U3, U5 | MAX4239AUT
21 | 1 | U4 | TMC6100-LA
22 | 1 | U6 | TPS560430XDBVR
23 | 1 | Y1 | 8MHz

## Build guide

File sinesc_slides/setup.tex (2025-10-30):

\documentclass[10pt,xcolor={dvipsnames}]{beamer}

\usepackage{amsmath}
\usepackage{amssymb}
\usepackage{graphicx}
%\usepackage{framed}
\usepackage[american]{circuitikz}
%\usepackage{pgfplots}
\usetikzlibrary{arrows.meta,overlay-beamer-styles,positioning,calc,fit}
%\usepackage[american]{circuitikz}
\usepackage{siunitx}
\usepackage[T1]{fontenc}
\usepackage{subcaption}
%\usepackage{mathtools}
%\usepackage{makecell}
%\usepackage{steinmetz}
%\usepackage{calc}

% set default graphics path to ``figs''
\graphicspath{{figs}}

\beamertemplatenavigationsymbolsempty
\setbeamertemplate{footline}{%
	\raisebox{10pt}{\makebox[\paperwidth]{\hfill\makebox[30pt]{\scriptsize\insertframenumber}}}}

%\pgfplotsset{compat=newest}
%\tikzset{>=Stealth}
%\pgfplotsset{
%	standard/.style={
%		trig format=rad,
%		axis x line=middle,
%		axis y line=middle,
%		enlarge x limits=0.15,
%		enlarge y limits=0.15,
%		x label style={right},
%		y label style={above},
%		y tick label style={right},
%		axis line style={-Stealth,semithick},
%		major tick style={thick,black},
%		extra x tick labels={\empty},
%		extra y tick labels={\empty}
%	}
%}

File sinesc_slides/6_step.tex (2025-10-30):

\begin{tikzpicture}[scale=0.5, >=Latex]
	\def\R{3}        % circle radius
	\def\arrlen{2.0} % tangent arrow length
	\def\n{6}        % number of tangent arrows (must be even)
	\def\rot{30}     % rotate phase axes CCW
	
	% Circle
	\draw[thick] (0,0) circle (\R);
	
	% --- Rotated phase axes (no color), label ends with x ---
	\foreach \ang/\labela/\labelb in {90+\rot/2/5, 210+\rot/4/1, 330+\rot/6/3}{
		\draw (0,0) -- ({\R*cos(\ang)},{\R*sin(\ang)});
		\draw (0,0) -- ({-\R*cos(\ang)},{-\R*sin(\ang)});
		\node at ({1.2*\R*cos(\ang)},{1.2*\R*sin(\ang)}) {$\labela$};
		\node at ({-1.2*\R*cos(\ang)},{-1.2*\R*sin(\ang)}) {$\labelb$};
	}
	
	% --- Fixed reference lines at 90°, 210°, 330° labeled U, V, W ---
	\foreach \ang/\name/\pos/\clr in {90/U/above/Red, 210/V/below left/Green, 330/W/below right/blue}{
		\draw[very thick,\clr] (0,0) -- ({\R*cos(\ang)},{\R*sin(\ang)});
		\node[\pos] at ({1.15*\R*cos(\ang)},{1.15*\R*sin(\ang)}) {\textcolor{\clr}{\name}};
	}
	
	% --- Tangent arrows (keep +30° base; rotate by \rot) ---
	% tangent at angle θ is (-sin θ, cos θ)
	\pgfmathtruncatemacro{\nm}{\n-1}
	\foreach \k in {0,...,\nm}{
		\pgfmathsetmacro{\ang}{30+\rot + 360/\n*\k}
		\pgfmathsetmacro{\px}{\R*cos(\ang)}
		\pgfmathsetmacro{\py}{\R*sin(\ang)}
		\pgfmathsetmacro{\tx}{-sin(\ang)}
		\pgfmathsetmacro{\ty}{ cos(\ang)}
		\draw[->] (\px,\py) -- ({\px+\arrlen*\tx},{\py+\arrlen*\ty});
	}
	
	% --- Diameters through opposite tangent points (same +30° base) ---
	\pgfmathtruncatemacro{\nhalf}{\n/2}
	\pgfmathtruncatemacro{\nhalfmone}{\nhalf-1}
	\foreach \k in {0,...,\nhalfmone}{
		\pgfmathsetmacro{\ang}{30+\rot + 360/\n*\k}
		\pgfmathsetmacro{\angOpp}{\ang+180}
		\pgfmathsetmacro{\px}{\R*cos(\ang)}
		\pgfmathsetmacro{\py}{\R*sin(\ang)}
		\pgfmathsetmacro{\qx}{\R*cos(\angOpp)}
		\pgfmathsetmacro{\qy}{\R*sin(\angOpp)}
		\draw[Latex-Latex] (\px,\py) -- (\qx,\qy);
	}
	
	% CCW rotation arc outside the circle
	\draw[->,thick] ({\R+1.2},0) arc[start angle=0,end angle=60,radius=\R+1.2];
\end{tikzpicture}

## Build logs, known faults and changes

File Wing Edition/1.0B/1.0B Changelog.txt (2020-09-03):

---------------------------
   SinESC Wing Edition   
v1.0A --> v1.0B CHANGELOG
---------------------------

* Updated component placement
* Updated silkscreen
* Changed LED from red 0201 to blue 0402
* Changed LED resistor from 220Ω to 120Ω for BOM consolidation
* Changed bus voltage monitor clamping diode from BAT30F4 0201 to BAT30KFILM SOD-523

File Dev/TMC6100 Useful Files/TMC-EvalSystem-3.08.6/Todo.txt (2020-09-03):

******************
ToDo:

CHECK 3:	Determine maximum Vel/Acc values for all chips & add those

REM 3:		Remove the deInit() functions and any deInit logic - we do not support unplugging an evaluation module without
            requiring a firmware restart.

ADD 2:		Single wire UART is asynchronous and has the potential for race conditions including both sides sending. Currently
			a per-chip workaround is implemented that adds a delay but this should be done properly in the UART.c files.

ADD 2:      Modify the StepDir Generator to allow running with any chip supporting StepDir. (LH)

CHECK 2:	Change function pointers that never change to normal functions (mostly in HAL, stuff like HAL.IOs->config->isHigh())

CHECK 2:	Check for useless usage of volatile. We shouldnt blindly declaring volatile until it works, but sometimes do.

CHECK 2:	#include path cleanup (avoid cyclic includes) (LH)

QOL 2:		Change Landungsbrücke/Startrampe selection to a gcc commandline define instead of makeFor.h files?

QOL 1:		Check comments - remove old ones, check for typo's, unclear messages etc. (LH)

******************
Zur Formatierung der inline-ToDo's:
Jedes Todo sollte ein Kommentar sein, auch wenn es hinter einem Kommentar steht
	z.B switch(mode) // Modusauswahl // todo: Variable umbenennen

Es sollte nichts hinter einem ToDo in der gleichen Zeile stehen, was nicht Teil des ToDo's ist

Bestimmte Sonderzeichen (z.B. *) sorgen dafür, dass in der Eclipse-ToDo-Liste der ToDo nur bis vor dem Sonderzeichen angezeigt wird - unbedingt vermeiden.

Format von Inline ToDo's:
// todo [Kategorie] [Priorität]: [Beschreibung] [(Autor)] [#Nummerierung]

	Kategorie:
		Stichwort, was das ToDo beinhaltet. Es können auch mehrere Stichworte genutzt werden, möglichst aber nur eins.
		Beispiele für Stichwörter:
			API		Änderungen im Zusammenhang mit der TMC-API
			ADD		Hinzufügen neuer Features/Funktionen etc.
			BUG		Programmfehler
			LOW		Low-Level Konfiguration oä. (in den Prozessor-Dateien)
			QOL 	Quality of life - Formatierung anpassen, Codestruktur ändern, Makros oder #define-Konstanten einbauen, umbenennen oä
			REM		Entfernen überflüssiger Features/Funktionen etc.
			XML		XML Dateien müssen angepasst/verglichen werden
			// 		ToDo ist zurzeit irrelevant, sollte aber nicht gelöscht werden - z.B. in auskommentiertem Code

	Priorität (Optional):
		Zahl zwischen 1 und 5. Keine Zahl entspricht niedrigster Priorität (1):
			5: Kritisch 		- Vollständiger Softwarecrash oä. - so früh wie möglich drum kümmern
			4: Gefährlich 		- Softwarecrash bei sehr speziellen Bedingungen, Fehlfunktion oä. (z.B. Motor wechselt abrupt Geschwindigkeiten)
			3: Normal			- Durchschnittliche Priorität, sollte vor Release erledigt sein
			2: Gering			- Leicht umgehbare Fehlfunktion des Programms, strukturelle Umstellung
			1: Nebensache		- Variablen umbenennen, Einrückung oä. schöner formatieren - Sachen die auf jeden Fall warten können

	Beschreibung:
		Hauptteil der Todo-Notiz

	Autor (Optional):
		Initialen des Verfassers des ToDo's. Vor allem bei hohen Prioritäten dazuschreiben

	Nummerierung (Optional):
		Sollte ein ToDo wiederholt auftreten (z.B. an mehreren cases in einem switch() ),
		so kann man hinter alles andere im ToDo eine Nummerierung ergänzen,
		sodass bei späterer Bearbeitung sofort erkennbar ist, dass man wiederholt gleiche Änderungen vorzunehmen hat.
		Am besten den ToDo-Text an allen Stellen komplett identisch lassen, so ist es am leichtesten zusammenzuhalten

Beispiele:
// todo XML 3: read/Write in XML Datei korrigieren (LH)

// todo QOL 2: MaskShift Makro manuell ergänzen (LK) #1
// todo QOL 2: MaskShift Makro manuell ergänzen (LK) #2
// todo QOL 2: MaskShift Makro manuell ergänzen (LK) #3

// todo BUG 4: Anschließen von diesem Board hängt die Landungsbrücke auf (EK)

// todo BUG 5: Landungsbrücke startet nicht, da hier falsch initialisiert wird. (LH)

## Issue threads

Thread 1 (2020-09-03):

Redesign Wing Edition in KiCad, adhere to OSHPark design rules, improve thermal and high-current layout

SAR-mango, 2020-09-03:
Wing Edition was originally designed in EasyEDA to JLCPCB specifications, but the new standard fab for prototype SinESC boards is OSHPark. Their tolerances are much tighter, making PCB layout much easier.
Thermal relief and high-current traces need to be improved to match Multi Edition.

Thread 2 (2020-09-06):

[MULTI] Fix MCU resonator circuit

SAR-mango, 2020-09-06:
Change the resonator to part CSTNE8M00G55Z000R0 for reduced cost and interchangeable pins.

A resistor of approximately 220Ω must be added between F1/OSC_OUT on the MCU (Pin 6) and one end of the resonator (Pin 1 or 3). BOM consolidation must be considered.

A parallel resistor across the resonator may also be required.

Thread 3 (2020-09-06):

Changes for production

SAR-mango, 2020-09-06:
The following changes are required before Multi Edition may be produced:
- The design rules of the production manufacturer will almost certainly differ from the current rules, so redesign the board to those new specifications (likely 6/6 mil trace/space with blind/buried vias). Try to retain current component placement.
- Switch to the 6-TDFN-EP version of the MAX4239 only if possible (currently there are vias under those chips since there are no exposed pads)
- Decrease BOM cost where possible (most notably, find cheaper passives)
- Panelize board
- Do anything else required for production (this issue will be updated as more production requirements arise)

SAR-mango, 2021-01-04:
*Planning some major design changes; this issue will be kept closed for now.

Closed 2021-01-04.

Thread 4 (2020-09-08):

[WING 2.0B] Changes for production

SAR-mango, 2020-09-08:
The following changes are required before Wing Edition may be produced, and mark the first production version of Wing Edition (these are the same as changes for Multi 2.4B):

- Reroute all traces with blind/buried vias and 6 mil trace/space minimum rules. NO COMPONENT PLACEMENT OR BOM CHANGES!
- Update inner layers and bottom layer for high power (wider traces).
- Update thermal design.
- Ensure BOM is not unnecessarily expensive.
- Panelize board.

Closed 2020-09-08.

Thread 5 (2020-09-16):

PCB improvements

SAR-mango, 2020-09-16:
To increase reliability at high current and to increase thermal performance:
- Add extra vias to high-current traces
- Add thermal vias where possible
- Enlarge & add more filled zones

For cosmetic purposes only:
- Make via clusters more uniform
- Trace shape conditioning
- Label PCB sections on the silkscreen

**Edit (New Year's Eve, 2020):** two major schematic issues have been fixed as well, and PCB and exported files have been updated to match the latest schematic. v2.3C should now work flawlessly, and software will be finalized after thorough testing and efficiency measurements.

Closed 2020-12-31.

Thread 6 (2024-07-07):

Mosfet proposal

LukasHNZ, 2024-07-07:
What about the https://www.infineon.com/cms/en/product/power/mosfet/n-channel/isg0613n04nm6hsc/ ? it got less resistance and lower gate capacitance. There are also other ones with a bit higher capacitance and lower resistance or vice versa. What do you think is the best tradeoff? Nexperia also got some very low resistance mosfets.

As I understood, a lower Resistance and faster switching would result in less Thermal losses, thus saving weight for cooling and increasing flight time both ways. Looking forward to hearing your perspective!

SAR-mango, 2024-07-07:
Glad to see interest in the project even after several years! May I ask what brought you here?

The FET you suggest is a great option. It didn't exist when I did the parts selection (four years ago), but I found that considering the _product_ of the gate charge and on-resistance helped me narrow down the options greatly. This FET excels in that regard.

When selecting parts for a new version of the ESC, I am going to consider the avalanche energy rating – this is crucial for durability. I may even switch to 60-volt FETs since 6S seems quite common these days (though I have sadly not kept up with the hobby since college began). I might also prioritize gate charge over on resistance, since I feel like I overestimated the peak and average motor currents. 55A seems overkill.

When developing the ESC into its current state, I mostly focused on the hardware. But when I revive the project, I am going to spend lots of time creating my own control algorithms. Partly because I now have some theoretical background, and partly because this is arguably more important than the hardware alone. I would be able to tailor the code for this exact application, cut out the useless garbage, and potentially stop using ST's HAL library. I also want to develop a self-tuning regime since I hate the idea of having to tune PIDs for each ESC/motor combination.

LukasHNZ, 2024-07-08:
What brought me here is google! I recently saw a ton of videos regarding a fpv speed record, reaching 500kph for a few seconds, also the Redbull drone that could stay at high speeds for relatively long times. Then the recent hype around special rotor shapes like from lifeline or toroidal propellers. I was wondering what the technological limits are at the time and how  it can be harvested! Some motor controllers on the market already use Vector control (FOC) - is this a synonym for the sinusoidal one you got or are there still differences? It also claims better efficiency, low end torque, less noise etc. but at a hefty pricetag usually.

If there is a significant difference between your approach and a FOC approach ill probably end up testing both, i was considering using a generic motor with any prop that usually goes with it, and then testing stationary thrust with a small rig with a load cell to find out how the real life figures are. With the current batteries energy density and the power hungry nature of UAVs every % of energy savings is very valuable- especially when going for record attempts or other extremes

SAR-mango, 2024-07-10:
There are differences between FOC and sinusoidal control. FOC is theoretically superior. It involves determining the exact rotor position and energizing the motor phases such that the magnetic field is exactly orthogonal to the rotor, which maximizes torque (and thus efficiency) and smoothness. I say theoretically because measuring the rotor position is difficult and usually requires a sensor. Sensorless techniques also exist, but require lots of tuning, precise current measurement circuitry, and well-designed software.

SinESC performs sensorless FOC. In the readme I used "sinusoidal control" and "FOC" interchangeably, but they are not the same. For certain motor types, FOC _results_ in a sinusoidal waveform. In these cases, one can do away with FOC and recreate the sinusoidal waveform "blindly". That is what sinusoidal control is. Nevertheless, I hope to develop the ESC to the point where it becomes ubiquitous within the hobby.

My expertise is EE and I hope to do my part to create the most efficient ESC, but there are probably better places to save energy. You should first optimize your overall avionics system and ensure that none of the subsystems draw a ton of extra power (example: choose an efficient video transmitter set to the minimum RF output power necessary). Then look into the mechanical and aerodynamics stuff – frame, prop airfoil, prop/motor combo, motors themselves. The greatest savings will probably be found there.

SAR-mango, 2025-07-22:
The enthusiasm is very much appreciated, but the project still requires lots of hardware and software development to be usable on a drone. I do not recommend ordering it on JLC in its current state. Realistically, I hope to turn this into a finished product by mid 2027.

I do plan to look into GaN FETs, but they are unlikely to provide much benefit. My current understanding is that GaN FETs are more expensive and more delicate than Si FETs, and would only provide a notable efficiency improvement if the switching frequency were in the MHz range. ESCs don't use such high switching frequencies, but I will investigate the effect of switching frequency and determine whether higher is better.

olekse, 2025-07-22:
@SAR-mango Thank you for the reply. I understand that you don't want me or anybody to think that you vouching for reliability of this board in its current state of development, however, for me personally, it's not the highest of concern, as I see this technology to be a no be clearly superior at least for uses that are relevant for me so I can sacrifice reliability. You don't recommend ordering but it should work right? But it is somewhat buggy at the moment, am I correct?

SAR-mango, 2025-07-22:
It will work, but far too unreliably for any application. The gate driver keeps dying because the charge pump output is missing a lowpass filter. Also, the current sensing is very noisy because the 50A rating is too high. This makes the position measurement ineffective, so the FOC algorithm struggles to commutate the motor reliably. Also, the firmware in the repository is a useless mess, and the ST library that it utilizes is five years old.

If you really want to try it out for development purposes, the bare-minimum changes you'd need to implement are:
- Redesign the PCB to something bigger, easier to debug, and more manufacturable
- Change the gate driver to something simpler such as the DGD2104MS8 (you'd need three of them)
- Redesign the current sensing for a lower maximum current, such that you can use 10-milliohm sense resistors
- Select FETs that have a much lower gate charge and slightly higher on-resistance
- Create new firmware, starting from the current version of ST's sensorless FOC library

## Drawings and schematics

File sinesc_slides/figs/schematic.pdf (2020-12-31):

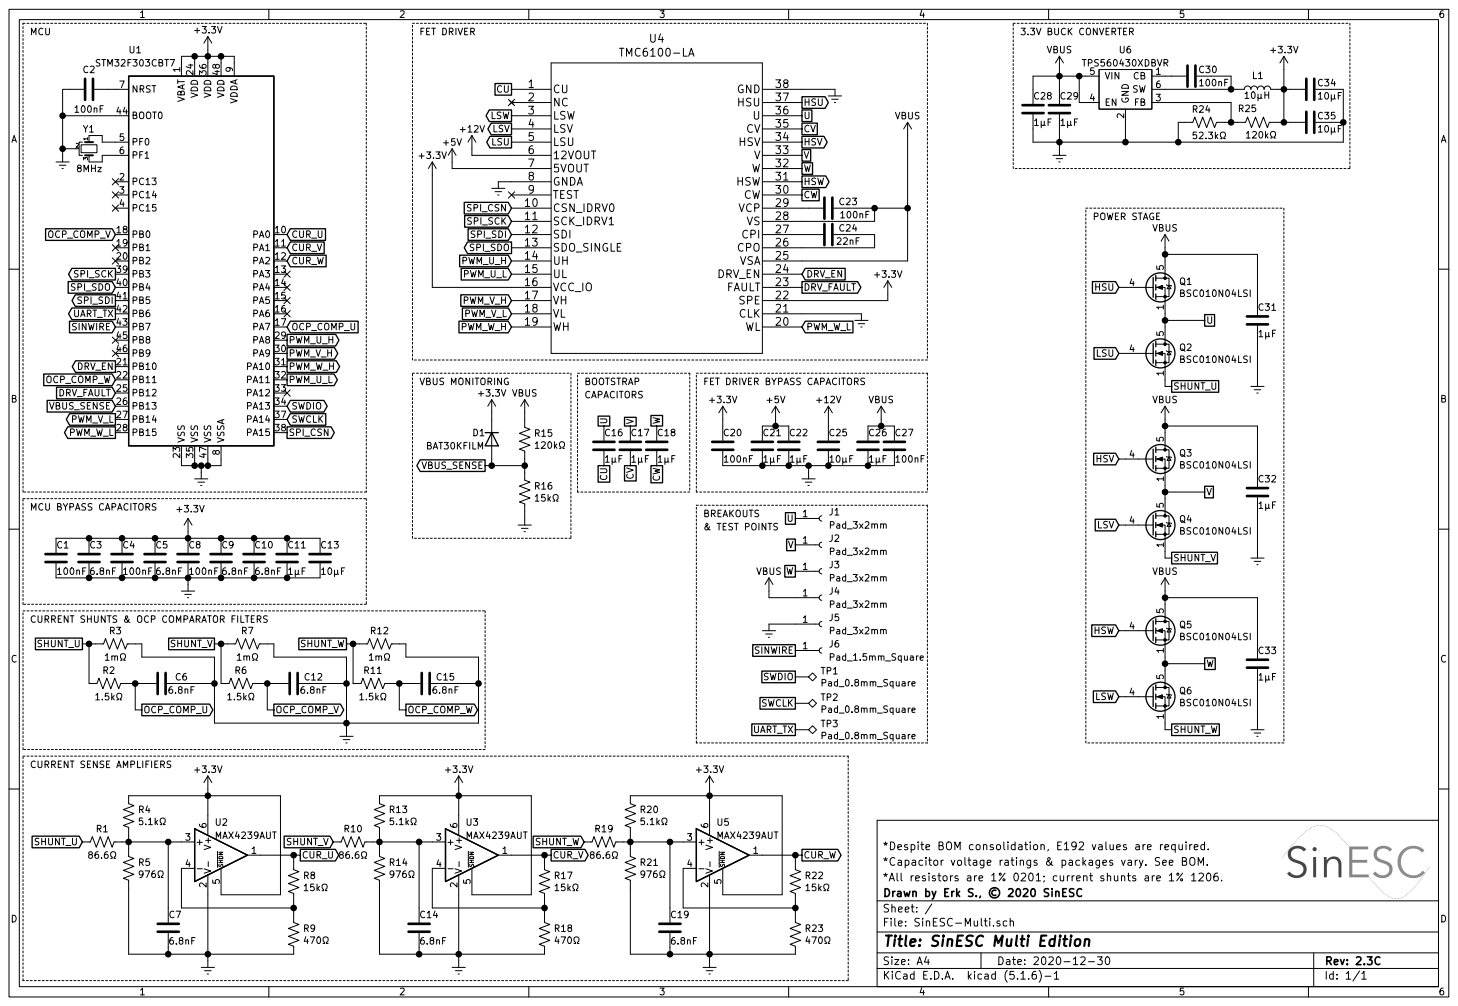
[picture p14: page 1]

2 FB 3 EN 4 VIN 5 SW 6 U6 TPS560430XDBVR

1 VDD 24 VDD 36 VDD 48 VDDA

9 VSS 23 VSS 35 VSS 47 VSSA

DRV_EN
PWM_W_L PWM_V_L VBUS_SENSE DRV_FAULT OCP_COMP_W
BOOTSTRAP CURRENT SHUNTS & OCP COMPARATOR FILTERS CURRENT SENSE AMPLIFIERS

*Capacitor voltage ratings & packages vary. See BOM.
*All resistors are 1% 0201; current shunts are 1% 1206.
File: SinESC-Multi.sch Sheet: / Drawn by Erk S., © 2020 SinESC

Id: 1/1 Title: SinESC Multi Edition

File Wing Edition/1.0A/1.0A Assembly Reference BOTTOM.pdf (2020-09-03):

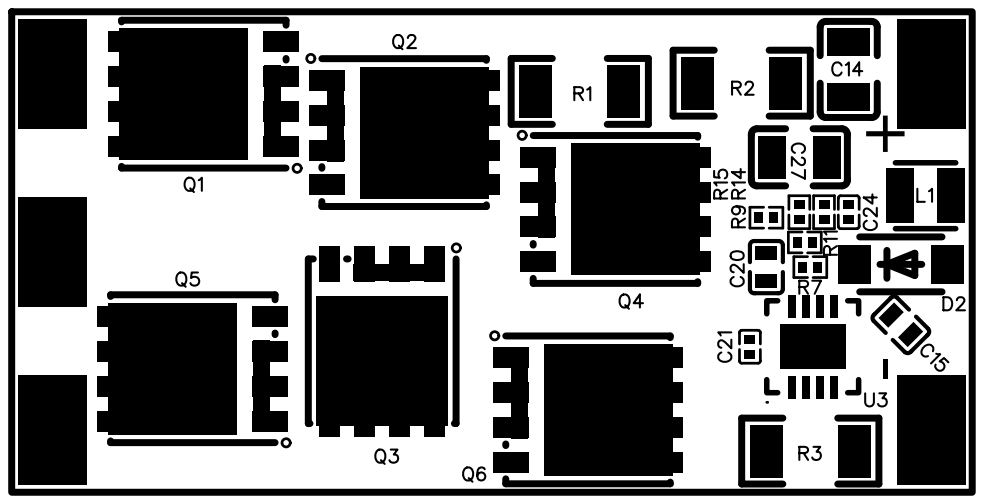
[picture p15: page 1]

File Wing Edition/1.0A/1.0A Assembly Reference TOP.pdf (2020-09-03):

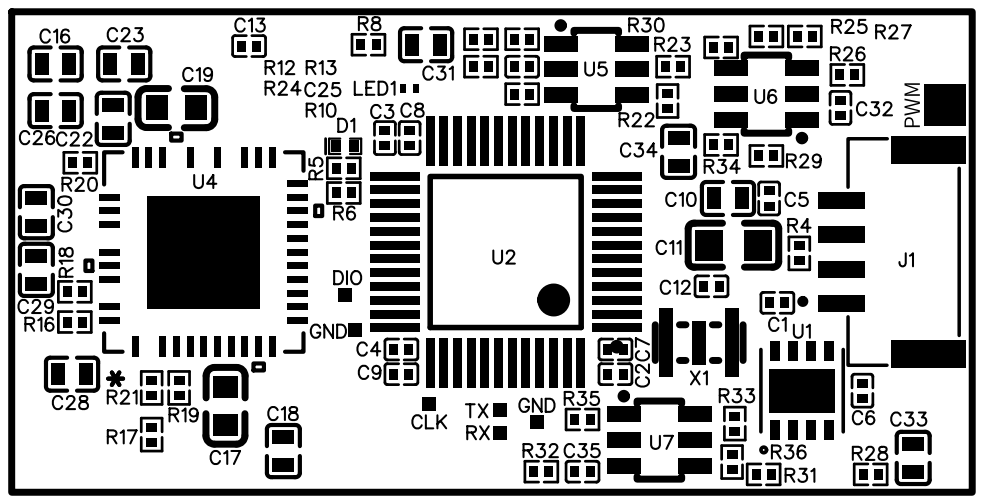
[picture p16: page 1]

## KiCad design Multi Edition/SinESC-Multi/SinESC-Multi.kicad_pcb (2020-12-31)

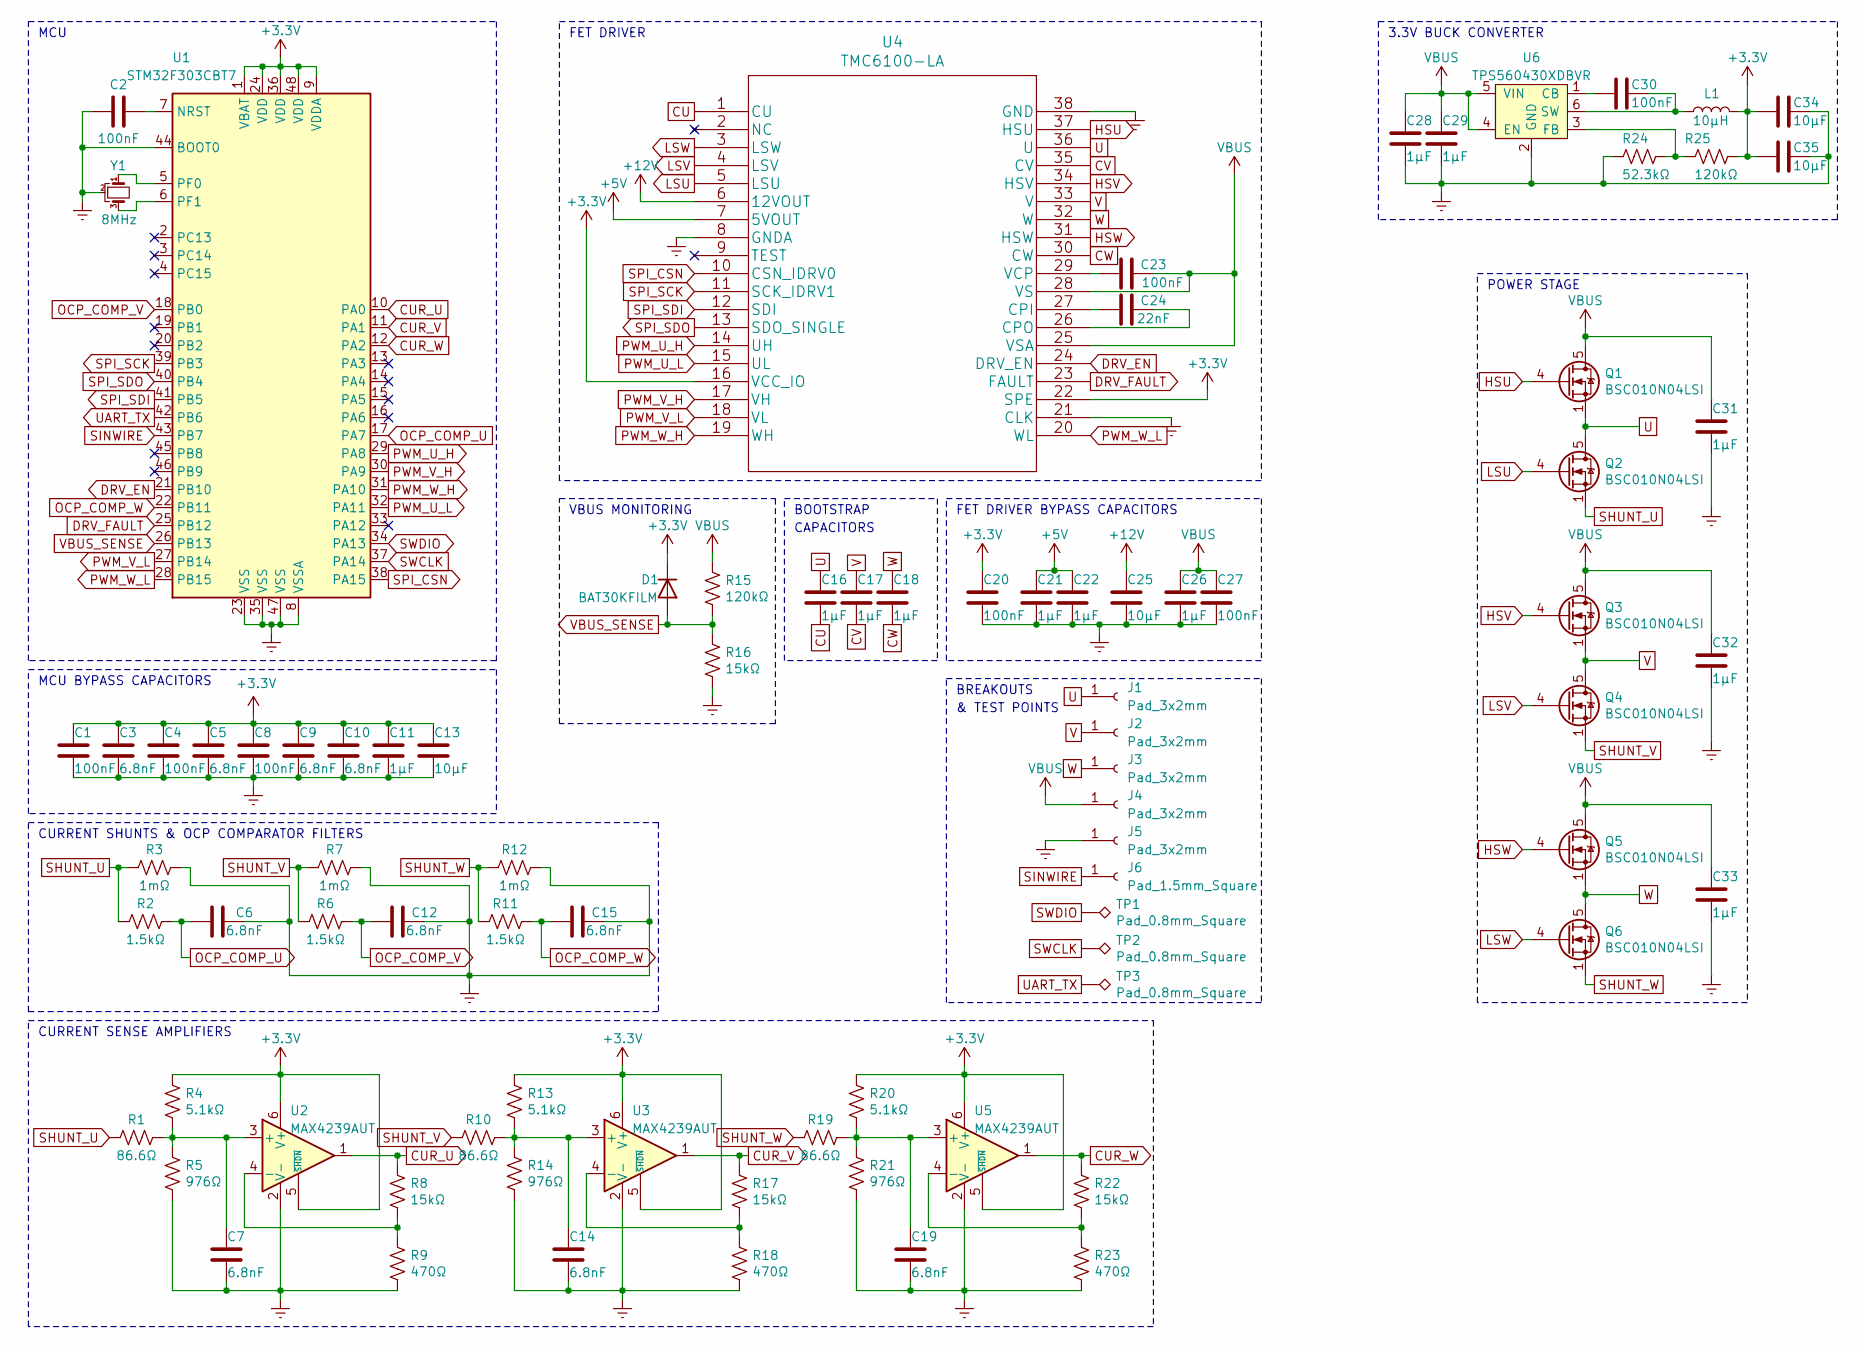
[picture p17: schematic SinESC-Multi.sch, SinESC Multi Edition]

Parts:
C1, C2, C4, C8, C20, C23: 100nF; C_0201_0603Metric; Voltage Rating 25V; Manufacturer Part # C0603X5R1E104K030BB
C3, C5, C6, C7, C9, C10, C12, C14, C15, C19: 6.8nF; C_0201_0603Metric; Voltage Rating 25V; Manufacturer Part # GRM033R71E682KE14D
C11, C16, C17, C18, C21, C22, C26, C31, C32, C33: 1µF; C_0402_1005Metric; Voltage Rating 50V; Manufacturer Part # UMK105CBJ105MV-F
C13, C25: 10µF; C_0603_1608Metric; Voltage Rating 25V; Manufacturer Part # C1608X5R1E106M080AC
C24: 22nF; C_0603_1608Metric; Voltage Rating 100V; Manufacturer Part # C1608X7R2A223K080AA
C27: 100nF; C_0402_1005Metric; Voltage Rating 50V; Manufacturer Part # C1005X7R1H104K050BB
C28, C29: 1µF; C_0402_1005Metric; Manufacturer Part # UMK105CBJ105MV-F
C30: 100nF; C_0201_0603Metric; Manufacturer Part # C0603X5R1E104K030BB
C34, C35: 10µF; C_0603_1608Metric; Manufacturer Part # C1608X5R1E106M080AC
D1: BAT30KFILM; D_SOD-523; Manufacturer Part # BAT30KFILM
J1, J2, J3, J4, J5: Pad_3x2mm
J6: Pad_1.5mm_Square
L1: 10µH; L_1210_3225Metric; Manufacturer Part # CBC3225T100KR
Q1, Q2, Q3, Q4, Q5, Q6: BSC010N04LSI; TDSON-8-1; Manufacturer Part # BSC010N04LSIATMA1
R1, R10, R19: 86.6Ω; R_0201_0603Metric; Manufacturer Part # ERJ-1GNF86R6C
R2, R6, R11: 1.5kΩ; R_0201_0603Metric; Manufacturer Part # ERJ-1GNF1501C
R3, R7, R12: 1mΩ; R_1206_3216Metric; Manufacturer Part # CSR1206-0R001F1
R4, R13, R20: 5.1kΩ; R_0201_0603Metric; Manufacturer Part # ERJ-1GNF5101C
R5, R14, R21: 976Ω; R_0201_0603Metric; Manufacturer Part # ERJ-1GNF9760C
R8, R16, R17, R22: 15kΩ; R_0201_0603Metric; Manufacturer Part # ERJ-1GNF1502C
R9, R18, R23: 470Ω; R_0201_0603Metric; Manufacturer Part # ERJ-1GNF4700C
R15, R25: 120kΩ; R_0201_0603Metric; Manufacturer Part # ERJ-1GNF1203C
R24: 52.3kΩ; R_0201_0603Metric; Manufacturer Part # ERJ-1GNF5232C
TP1, TP2, TP3: Pad_0.8mm_Square
U1: STM32F303CBT7; LQFP-48_7x7mm_P0.5mm_narrow_pads; Manufacturer Part # STM32F303CBT7
U2, U3, U5: MAX4239AUT; SOT-23-6; Manufacturer Part # MAX4239AUT+T
U4: TMC6100-LA; Manufacturer Part # TMC6100-LA-T
U6: TPS560430XDBVR; SOT-23-6; Manufacturer Part # TPS560430XDBVR
Y1: 8MHz; Resonator_SMD_muRata_CSTxExxV-3Pin_3.0x1.1mm; Manufacturer Part # CSTNE8M00G550000R0

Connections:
+3V3: C1.1, C3.1, C4.1, C5.1, C8.1, C9.1, C10.1, C11.1, C13.1, C20.1, C34.2, C35.2, D1.1 (K), L1.2, R4.1, R13.1, R20.1, R25.2, U1.1 (VBAT), U1.9 (VDDA), U1.24 (VDD), U1.36 (VDD), U1.48 (VDD), U2.5 (~SHDN), U2.6 (V+), U3.5 (~SHDN), U3.6 (V+), U4.16 (VCC_IO), U4.22 (SPE), U5.5 (~SHDN), U5.6 (V+)
+5V: C21.1, C22.1, U4.7 (5VOUT)
+12V: C25.1, U4.6 (12VOUT)
CU: C16.2, U4.1 (CU)
CUR_U: R8.1, U1.10 (PA0), U2.1
CUR_V: R17.1, U1.11 (PA1), U3.1
CUR_W: R22.1, U1.12 (PA2), U5.1
CV: C17.2, U4.35 (CV)
CW: C18.2, U4.30 (CW)
DRV_EN: U1.21 (PB10), U4.24 (DRV_EN)
DRV_FAULT: U1.25 (PB12), U4.23 (FAULT)
Earth: C1.2, C2.2, C3.2, C4.2, C5.2, C6.1, C7.2, C8.2, C9.2, C10.2, C11.2, C12.1, C13.2, C14.2, C15.1, C19.2, C20.2, C21.2, C22.2, C25.2, C26.2, C27.2, C28.2, C29.2, C31.2, C32.2, C33.2, C34.1, C35.1, J5.1, R3.1, R5.2, R7.1, R9.2, R12.1, R14.2, R16.2, R18.2, R21.2, R23.2, R24.2, U1.8 (VSSA), U1.23 (VSS), U1.35 (VSS), U1.44 (BOOT0), U1.47 (VSS), U2.2 (V-), U3.2 (V-), U4.8 (GNDA), U4.21 (CLK), U4.38 (GND), U5.2 (V-), U6.2 (GND), Y1.2
HSU: Q1.4 (G), U4.37 (HSU)
HSV: Q3.4 (G), U4.34 (HSV)
HSW: Q5.4 (G), U4.31 (HSW)
LSU: Q2.4 (G), U4.5 (LSU)
LSV: Q4.4 (G), U4.4 (LSV)
LSW: Q6.4 (G), U4.3 (LSW)
unnamed: C2.1, U1.7 (NRST)
unnamed: C7.1, R1.1, R4.2, R5.1, U2.3 (+)
unnamed: C14.1, R10.1, R13.2, R14.1, U3.3 (+)
unnamed: C19.1, R19.1, R20.2, R21.1, U5.3 (+)
unnamed: C23.2, U4.29 (VCP)
unnamed: C24.1, U4.26 (CPO)
unnamed: C24.2, U4.27 (CPI)
unnamed: C30.1, L1.1, U6.6 (SW)
unnamed: C30.2, U6.1 (CB)
unnamed: R8.2, R9.1, U2.4 (-)
unnamed: R17.2, R18.1, U3.4 (-)
unnamed: R22.2, R23.1, U5.4 (-)
unnamed: R24.1, R25.1, U6.3 (FB)
unnamed: U1.5 (PF0), Y1.1
unnamed: U1.6 (PF1), Y1.3
OCP_COMP_U: C6.2, R2.1, U1.17 (PA7)
OCP_COMP_V: C12.2, R6.1, U1.18 (PB0)
OCP_COMP_W: C15.2, R11.1, U1.22 (PB11)
PWM_U_H: U1.29 (PA8), U4.14 (UH)
PWM_U_L: U1.32 (PA11), U4.15 (UL)
PWM_V_H: U1.30 (PA9), U4.17 (VH)
PWM_V_L: U1.27 (PB14), U4.18 (VL)
PWM_W_H: U1.31 (PA10), U4.19 (WH)
PWM_W_L: U1.28 (PB15), U4.20 (WL)
SHUNT_U: Q2.1 (S), Q2.2 (S), Q2.3 (S), R1.2, R2.2, R3.2
SHUNT_V: Q4.1 (S), Q4.2 (S), Q4.3 (S), R6.2, R7.2, R10.2
SHUNT_W: Q6.1 (S), Q6.2 (S), Q6.3 (S), R11.2, R12.2, R19.2
SINWIRE: J6.1, U1.43 (PB7)
SPI_CSN: U1.38 (PA15), U4.10 (CSN_IDRV0)
SPI_SCK: U1.39 (PB3), U4.11 (SCK_IDRV1)
SPI_SDI: U1.41 (PB5), U4.12 (SDI)
SPI_SDO: U1.40 (PB4), U4.13 (SDO_SINGLE)
SWCLK: TP2.1, U1.37 (PA14)
SWDIO: TP1.1, U1.34 (PA13)
U: C16.1, J1.1, Q1.1 (S), Q1.2 (S), Q1.3 (S), Q2.5 (D), U4.36 (U)
UART_TX: TP3.1, U1.42 (PB6)
V: C17.1, J2.1, Q3.1 (S), Q3.2 (S), Q3.3 (S), Q4.5 (D), U4.33 (V)
VBUS: C23.1, C26.1, C27.1, C28.1, C29.1, C31.1, C32.1, C33.1, J4.1, Q1.5 (D), Q3.5 (D), Q5.5 (D), R15.1, U4.25 (VSA), U4.28 (VS), U6.4 (EN), U6.5 (VIN)
VBUS_SENSE: D1.2 (A), R15.2, R16.1, U1.26 (PB13)
W: C18.1, J3.1, Q5.1 (S), Q5.2 (S), Q5.3 (S), Q6.5 (D), U4.32 (W)

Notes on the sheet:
CURRENT SENSE AMPLIFIERS
CURRENT SHUNTS & OCP COMPARATOR FILTERS
FET DRIVER BYPASS CAPACITORS
FET DRIVER
MCU BYPASS CAPACITORS
MCU
POWER STAGE
BREAKOUTS
& TEST POINTS
VBUS MONITORING
3.3V BUCK CONVERTER
BOOTSTRAP
CAPACITORS

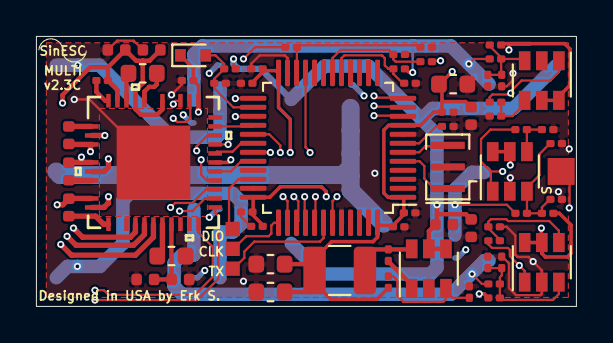
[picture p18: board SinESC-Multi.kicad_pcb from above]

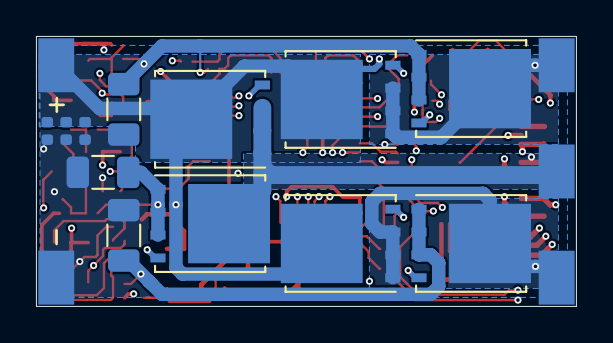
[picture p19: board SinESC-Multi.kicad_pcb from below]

Board: 4 copper layers, 30.0 x 15.0 mm, 84 parts (17 on the bottom side), 58 nets.

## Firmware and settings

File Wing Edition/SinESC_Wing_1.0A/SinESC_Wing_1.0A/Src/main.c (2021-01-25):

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
/* Includes ------------------------------------------------------------------*/
#include "main.h"
#include "motorcontrol.h"

/* USER CODE BEGIN Includes */
#include "stm32f3xx_hal.h"
/* USER CODE END Includes */

/* USER CODE BEGIN PD */

/* TMC6100 REGISTER LIST */
#define TMC6100_GCONF          	0x00
#define TMC6100_GSTAT          	0x01
#define TMC6100_IOIN		   	0x04
#define TMC6100_OTP_PROG       	0x06
#define TMC6100_OTP_READ       	0x07
#define TMC6100_FACTORY_CONF   	0x08
#define TMC6100_SHORT_CONF     	0x09
#define TMC6100_DRV_CONF       	0x0A

/* TMC6100 WRITE BYTE */
#define TMC6100_WRITE_BYTE		0x80

/* USER CODE END PD */

ADC_HandleTypeDef hadc1;
ADC_HandleTypeDef hadc3;

CAN_HandleTypeDef hcan;

COMP_HandleTypeDef hcomp2;
COMP_HandleTypeDef hcomp4;
COMP_HandleTypeDef hcomp6;

DAC_HandleTypeDef hdac;

SPI_HandleTypeDef hspi1;

TIM_HandleTypeDef htim1;
TIM_HandleTypeDef htim2;

UART_HandleTypeDef huart1;

/* USER CODE BEGIN PV */

/* Any data read from the TMC6100 driver chip will fill up the array.
 * While debugging, set breakpoints AFTER reading from a relevant register to view the data in this buffer.
 */
uint8_t SPIRxBuf [5];

/* Driver configuration */
/* First entry is MSB, last entry is LSB in SPI, when writing order is 0 to 3
 * Bit order is MSb___LSb */
uint8_t GCONF_Write [4] = {0x00, 0x00, 0x00, 0x40}; // {0x00, 0x00, 0x00, 0x40}; latest: {0x00, 0x00, 0x00, 0x82}
uint8_t SHORT_CONF_Write [4] = {0x12, 0x01, 0x05, 0x0A}; // {0x60, 0x01, 0x05, 0x0A}
uint8_t DRV_CONF_Write [4] = {0x00, 0x0c, 0x00, 0x00}; // {0x00, 0x0E, 0x00, 0x00}
uint8_t GSTAT_Write [4] = {0xFF, 0xFF, 0xFF, 0xFF};

/* USER CODE END PV */

void SystemClock_Config(void);
static void MX_GPIO_Init(void);
static void MX_ADC1_Init(void);
static void MX_ADC3_Init(void);
static void MX_COMP2_Init(void);
static void MX_COMP4_Init(void);
static void MX_COMP6_Init(void);
static void MX_TIM1_Init(void);
static void MX_TIM2_Init(void);
static void MX_USART1_UART_Init(void);
static void MX_CAN_Init(void);
static void MX_DAC_Init(void);
static void MX_SPI1_Init(void);
static void MX_NVIC_Init(void);
/* USER CODE BEGIN PFP */

void SPIread (uint8_t address, uint8_t *rxBuf);
void SPIwrite (uint8_t address, uint8_t *data);
void configureDriver (void);
void resetDriver (void);

/* USER CODE END PFP */

/**
  * @brief  The application entry point.
  * @retval int
  */
int main(void)
{
  /* MCU Configuration--------------------------------------------------------*/

  /* Reset of all peripherals, Initializes the Flash interface and the Systick. */
  HAL_Init();

  /* Configure the system clock */
  SystemClock_Config();

  /* Initialize all configured peripherals */
  MX_GPIO_Init();
  MX_ADC1_Init();
  MX_ADC3_Init();
  MX_COMP2_Init();
  MX_COMP4_Init();
  MX_COMP6_Init();
  MX_TIM1_Init();
  MX_TIM2_Init();
  MX_USART1_UART_Init();
  MX_MotorControl_Init();
  MX_CAN_Init();
  MX_DAC_Init();
  MX_SPI1_Init();

  /* Initialize interrupts */
  MX_NVIC_Init();
  /* USER CODE BEGIN 2 */
  
  /*Initialization of Electronic Speed Controller (STEVAL-ESC001V1)*/
  esc_boot(&ESC_M1);

  /* Reset the driver */
  resetDriver ();
  //SPIwrite (TMC6100_GSTAT, GSTAT_Write);
  SPIread (TMC6100_IOIN, SPIRxBuf);
  SPIread (TMC6100_GSTAT, SPIRxBuf);
  SPIread (TMC6100_GCONF, SPIRxBuf);
  SPIread (TMC6100_SHORT_CONF, SPIRxBuf);
  SPIread (TMC6100_DRV_CONF, SPIRxBuf);
  /* Write driver configuration to its registers through SPI */
  configureDriver ();

  /* DEBUG: read the registers after writing */
  SPIread (TMC6100_GCONF, SPIRxBuf);
  SPIread (TMC6100_SHORT_CONF, SPIRxBuf);
  SPIread (TMC6100_DRV_CONF, SPIRxBuf);

  /* USER CODE END 2 */

  /* Infinite loop */
  /* USER CODE BEGIN WHILE */
 /* MC_ProgramSpeedRampMotor1(150, 3000);

  MC_StartMotor1(); */

  while (1)
  {
    /* USER CODE END WHILE */

    /* USER CODE BEGIN 3 */

    /* Main routine for Electronic Speed Controller (STEVAL-ESC001V1) */
    esc_pwm_control(&ESC_M1); 

    /* Driver fault handling */
    // if (HAL_GPIO_ReadPin(GPIOB, GPIO_PIN_12)) {
    	if (0) {
    	/* Turn on fault LED */
    	HAL_GPIO_WritePin(GPIOB, GPIO_PIN_2, GPIO_PIN_SET);
    	/* DEBUG: read all input pins */
        SPIread (TMC6100_IOIN, SPIRxBuf);
        /* DEBUG: read fault register */
        SPIread (TMC6100_GSTAT, SPIRxBuf);
        /* Reset the driver */
        resetDriver ();
        /* DEBUG: read fault register */
        SPIread (TMC6100_GSTAT, SPIRxBuf);
        /* Write driver configuration to its registers through SPI */
        //configureDriver ();
/*    }
    else { */
    	/* Turn off fault LED */
    	HAL_GPIO_WritePin(GPIOB, GPIO_PIN_2, GPIO_PIN_RESET);
    }

   }
  /* USER CODE END 3 */
}

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
/* USER CODE BEGIN 4 */

void SPIread (uint8_t address, uint8_t *inputBuffer) {
	uint8_t outputBuffer [5] = {address, 0x00, 0x00, 0x00, 0x00};
	/* READ */
	/* Pull NSS LOW before beginning the transaction*/
	HAL_GPIO_WritePin(GPIOA, GPIO_PIN_15, GPIO_PIN_RESET);
	/* Transaction */
	HAL_SPI_TransmitReceive(&hspi1, outputBuffer, inputBuffer, 5, 1);
	/* Transaction is over; pull NSS HIGH once again */
	HAL_GPIO_WritePin(GPIOA, GPIO_PIN_15, GPIO_PIN_SET);
}

void SPIwrite (uint8_t address, uint8_t *data) {
	uint8_t outputBuffer [5] = {address + TMC6100_WRITE_BYTE, data [0], data [1], data [2], data [3]};
	uint8_t inputBuffer [5];
	/* READ */
	/* Pull NSS LOW before beginning the transaction*/
	HAL_GPIO_WritePin(GPIOA, GPIO_PIN_15, GPIO_PIN_RESET);
	/* Transaction */
	HAL_SPI_TransmitReceive(&hspi1, outputBuffer, inputBuffer, 5, 1);
	/* Transaction is over; pull NSS HIGH once again */
	HAL_GPIO_WritePin(GPIOA, GPIO_PIN_15, GPIO_PIN_SET);
}

void configureDriver (void) {
	SPIwrite (TMC6100_GCONF, GCONF_Write);
	SPIwrite (TMC6100_SHORT_CONF, SHORT_CONF_Write);
	SPIwrite (TMC6100_DRV_CONF, DRV_CONF_Write);
}

void resetDriver (void) {
	HAL_GPIO_WritePin(GPIOB, GPIO_PIN_10, GPIO_PIN_RESET);
	HAL_Delay (50);
	HAL_GPIO_WritePin(GPIOB, GPIO_PIN_10, GPIO_PIN_SET);
}

/* USER CODE END 4 */
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


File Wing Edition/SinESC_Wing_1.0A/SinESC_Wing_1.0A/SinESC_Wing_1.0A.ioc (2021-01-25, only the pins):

Mcu.UserName=STM32F303CBTx
PA0.GPIO_Label=M1_CURR_AMPL_U
PA0.Signal=ADC1_IN1
PA1.GPIO_Label=M1_CURR_AMPL_V
PA1.Signal=ADC1_IN2
PA10.GPIO_Label=M1_PWM_WH
PA10.Signal=S_TIM1_CH3
PA11.GPIO_Label=M1_PWM_UL
PA11.Signal=TIM1_CH1N
PA13.Signal=SYS_JTMS-SWDIO
PA14.Signal=SYS_JTCK-SWCLK
PA15.GPIO_Label=SPI1_NSS_SOFT
PA15.Signal=GPIO_Output
PA2.GPIO_Label=M1_CURR_AMPL_W
PA2.Signal=ADC1_IN3
PA4.Signal=COMP_DAC1_group
PA5.GPIO_Label=M1_PWM_INPUT
PA5.Signal=S_TIM2_CH1_ETR
PA7.GPIO_Label=M1_CURR_SHUNT_U
PA7.Signal=COMP2_INP
PA8.GPIO_Label=M1_PWM_UH
PA8.Signal=S_TIM1_CH1
PA9.GPIO_Label=M1_PWM_VH
PA9.Signal=S_TIM1_CH2
PB0.GPIO_Label=M1_CURR_SHUNT_V
PB0.Signal=COMP4_INP
PB10.GPIO_Label=DRV_EN
PB10.Signal=GPIO_Output
PB11.GPIO_Label=M1_CURR_SHUNT_W
PB11.Signal=COMP6_INP
PB12.GPIO_Label=DRV_FAULT
PB12.Signal=GPIO_Input
PB13.GPIO_Label=M1_BUS_VOLTAGE
PB13.Signal=ADC3_IN5
PB14.GPIO_Label=M1_PWM_VL
PB14.Signal=TIM1_CH2N
PB15.GPIO_Label=M1_PWM_WL
PB15.Signal=TIM1_CH3N
PB2.GPIO_Label=STAT_LED
PB2.Signal=GPIO_Output
PB3.Signal=SPI1_SCK
PB4.Signal=SPI1_MISO
PB5.Signal=SPI1_MOSI
PB6.GPIO_Label=UART_TX
PB6.Signal=USART1_TX
PB7.GPIO_Label=UART_RX
PB7.Signal=USART1_RX
PB8.Signal=CAN_RX
PB9.Signal=CAN_TX
PF0-OSC_IN.Signal=RCC_OSC_IN
PF1-OSC_OUT.Signal=RCC_OSC_OUT

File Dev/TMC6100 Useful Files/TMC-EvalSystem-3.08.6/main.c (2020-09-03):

#include "boards/Board.h"
#include "hal/derivative.h"
#include "hal/HAL.h"
#include "tmc/IdDetection.h"
#include "tmc/TMCL.h"
#include "tmc/VitalSignsMonitor.h"
#include "tmc/BoardAssignment.h"

const char *VersionString = MODULE_ID"V308"; // module id and version of the firmware shown in the TMCL-IDE

/* Keep as is! This lines are important for the update functionality. */
#if defined(Landungsbruecke)
	const uint8_t Protection[] __attribute__ ((section(".cfmconfig")))=
	{
		0xFF, 0xFF, 0xFF, 0xFF, 0xFF, 0xFF, 0xFF, 0xFF,  //Backdoor key
		0xFF, 0xFF, 0xFF, 0xFF,                          //Flash protection (FPPROT)
		0x7E,                                            //Flash security   (FSEC) => nach Image-Generierung manuell auf 0x40 setzen im Image
		0xF9,                                            //Flash option     (FOPT) (NMI ausgeschaltet, EzPort ausgeschaltet, Normal power)
		0xFF,                                            //reserved
		0xFF                                             //reserved
	};

	struct BootloaderConfig {
		uint32_t BLMagic;
		uint32_t drvEnableResetValue;
	};

	// This struct gets placed at a specific address by the linker
	struct BootloaderConfig __attribute__ ((section(".bldata"))) BLConfig;
#endif


/* Check if jumping into bootloader is forced                                           */
/*                                                                                      */
/* In order to jump to bootloader e.g. because of an accidental infinite loop           */
/* in a modified firmware you may short ID_CLK and ID_CH0 pins on start up.             */
/* This will force the entrance into bootloader mode and allow to replace bad firmware. */
void shallForceBoot()
{
	// toggle each pin and see if you can read the state on the other
	// leave if not, because this means that the pins are not tied together
	HAL.IOs->config->toOutput(&HAL.IOs->pins->ID_CLK);
	HAL.IOs->config->toInput(&HAL.IOs->pins->ID_CH0);

	HAL.IOs->config->setHigh(&HAL.IOs->pins->ID_CLK);
	if(!HAL.IOs->config->isHigh(&HAL.IOs->pins->ID_CH0))
		return;

	HAL.IOs->config->setLow(&HAL.IOs->pins->ID_CLK);
	if(HAL.IOs->config->isHigh(&HAL.IOs->pins->ID_CH0))
		return;

	HAL.IOs->config->toOutput(&HAL.IOs->pins->ID_CH0);
	HAL.IOs->config->toInput(&HAL.IOs->pins->ID_CLK);

	HAL.IOs->config->setHigh(&HAL.IOs->pins->ID_CH0);
	if(!HAL.IOs->config->isHigh(&HAL.IOs->pins->ID_CLK))
		return;

	HAL.IOs->config->setLow(&HAL.IOs->pins->ID_CH0);
	if(HAL.IOs->config->isHigh(&HAL.IOs->pins->ID_CLK))
		return;

	// not returned, this means pins are tied together
	tmcl_boot();
}

/* Call all standard initialization routines. */
static void init()
{
#if defined(Landungsbruecke)
	// Default value: Driver enable gets set high by the bootloader
	BLConfig.drvEnableResetValue = 1;
#endif

	HAL.init();                  // Initialize Hardware Abstraction Layer
	IDDetection_init();          // Initialize board detection
	tmcl_init();                 // Initialize TMCL communication

	tmcdriver_init();            // Initialize dummy driver board --> preset EvalBoards.ch2
	tmcmotioncontroller_init();  // Initialize dummy motion controller board  --> preset EvalBoards.ch1

	VitalSignsMonitor.busy = 1;  // Put state to busy
	Evalboards.driverEnable = DRIVER_ENABLE;
	Evalboards.ch1.id = 0;       // preset id for driver board to 0 --> error/not found
	Evalboards.ch2.id = 0;       // preset id for driver board to 0 --> error/not found

	// We disable the drivers before configurating anything
	HAL.IOs->config->toOutput(&HAL.IOs->pins->DIO0);
	HAL.IOs->config->setHigh(&HAL.IOs->pins->DIO0);

	IdAssignmentTypeDef ids = { 0 };
	IDDetection_initialScan(&ids);  // start initial board detection
	IDDetection_initialScan(&ids);  // start second time, first time not 100% reliable, not sure why - too fast after startup?
	if(!ids.ch1.id && !ids.ch2.id)
	{
		shallForceBoot();           // only checking to force jump into bootloader if there are no boards attached
		// todo CHECK 2: Workaround: shallForceBoot() changes pin settings - change them again here, since otherwise IDDetection partially breaks (LH)
		HAL.IOs->config->toOutput(&HAL.IOs->pins->ID_CLK);
		HAL.IOs->config->toInput(&HAL.IOs->pins->ID_CH0);

	}

	if (ID_CH1_DEFAULT && (!ids.ch1.id || ID_CH1_OVERRIDE))
	{
		ids.ch1.id = ID_CH1_DEFAULT;
		ids.ch1.state = ID_STATE_DONE;
	}

	if (ID_CH2_DEFAULT && (!ids.ch2.id || ID_CH2_OVERRIDE))
	{
		ids.ch2.id = ID_CH2_DEFAULT;
		ids.ch2.state = ID_STATE_DONE;
	}

	Board_assign(&ids);             // assign boards with detected id

	VitalSignsMonitor.busy 	= 0;    // not busy any more!
}

/* main function */
int main(void)
{
	// Start all initialization routines
	init();

	// Main loop
	while(1)
	{
		// Check all parameters and life signs and mark errors
		vitalsignsmonitor_checkVitalSigns();

		// Perodic jobs of Motion controller/Driver boards
		Evalboards.ch1.periodicJob(systick_getTick());
		Evalboards.ch2.periodicJob(systick_getTick());

		// Process TMCL communication
		tmcl_process();
	}

	return 0;
}

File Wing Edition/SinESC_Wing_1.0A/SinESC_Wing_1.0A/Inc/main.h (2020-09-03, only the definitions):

#define M1_CURR_AMPL_U_Pin GPIO_PIN_0
#define M1_CURR_AMPL_U_GPIO_Port GPIOA
#define M1_CURR_AMPL_V_Pin GPIO_PIN_1
#define M1_CURR_AMPL_V_GPIO_Port GPIOA
#define M1_CURR_AMPL_W_Pin GPIO_PIN_2
#define M1_CURR_AMPL_W_GPIO_Port GPIOA
#define M1_PWM_INPUT_Pin GPIO_PIN_5
#define M1_PWM_INPUT_GPIO_Port GPIOA
#define M1_CURR_SHUNT_U_Pin GPIO_PIN_7
#define M1_CURR_SHUNT_U_GPIO_Port GPIOA
#define M1_CURR_SHUNT_V_Pin GPIO_PIN_0
#define M1_CURR_SHUNT_V_GPIO_Port GPIOB
#define STAT_LED_Pin GPIO_PIN_2
#define STAT_LED_GPIO_Port GPIOB
#define DRV_EN_Pin GPIO_PIN_10
#define DRV_EN_GPIO_Port GPIOB
#define M1_CURR_SHUNT_W_Pin GPIO_PIN_11
#define M1_CURR_SHUNT_W_GPIO_Port GPIOB
#define DRV_FAULT_Pin GPIO_PIN_12
#define DRV_FAULT_GPIO_Port GPIOB
#define M1_BUS_VOLTAGE_Pin GPIO_PIN_13
#define M1_BUS_VOLTAGE_GPIO_Port GPIOB
#define M1_PWM_VL_Pin GPIO_PIN_14
#define M1_PWM_VL_GPIO_Port GPIOB
#define M1_PWM_WL_Pin GPIO_PIN_15
#define M1_PWM_WL_GPIO_Port GPIOB
#define M1_PWM_UH_Pin GPIO_PIN_8
#define M1_PWM_UH_GPIO_Port GPIOA
#define M1_PWM_VH_Pin GPIO_PIN_9
#define M1_PWM_VH_GPIO_Port GPIOA
#define M1_PWM_WH_Pin GPIO_PIN_10
#define M1_PWM_WH_GPIO_Port GPIOA
#define M1_PWM_UL_Pin GPIO_PIN_11
#define M1_PWM_UL_GPIO_Port GPIOA
#define SPI1_NSS_SOFT_Pin GPIO_PIN_15
#define SPI1_NSS_SOFT_GPIO_Port GPIOA
#define UART_TX_Pin GPIO_PIN_6
#define UART_TX_GPIO_Port GPIOB
#define UART_RX_Pin GPIO_PIN_7
#define UART_RX_GPIO_Port GPIOB

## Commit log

2020-09-03 Added remaining files
    [1.0A Capacitors.xlsx, 1.0A Final BOM for Assembly.xlsx, 1.0A Final BOM.xlsx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]
2020-09-03 Add 3D model of TMC6100
    [SinESC-Multi-1.0A.kicad_pcb]
2020-09-03 Add custom libraries and 3D renders
    [BOM.csv, SinESC-Multi-1.0A.csv, Standard Capacitor List.xlsx]
2020-09-03 PCB trace conditioning
    [SinESC-Multi-1.0A.kicad_pcb]
2020-09-03 Update version numbering and 3D renders
    [BOM.csv, SinESC-Multi-1.0A.kicad_pcb, SinESC-Multi-1.0A.sch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]
2020-09-03 Update 3D renders
    [SinESC-Multi-2.3B.kicad_pcb]
2020-09-03 Change TMC6100 attribute from through-hole to SMD
    [SinESC-Multi-2.3B.kicad_pcb]
2020-09-03 Update BOM
    [BOM.csv, BOM.xlsx]
2020-09-06 Add logo to schematic
    [SinESC-Multi-2.3B.sch]
2020-09-10 Add new logo to schematic
    [SinESC-Multi-2.3B.sch]
2020-09-10 Update schematic cosmetics
    [SinESC-Multi-2.3B.sch]
2020-09-16 Update logo
    [SinESC-Multi-2.3B.sch]
2020-09-17 Update R24 footprint & 3D model
    [SinESC-Multi-2.3B.kicad_pcb, SinESC-Multi-2.3B.sch]
2020-09-19 Create 2.3B Hand-Assembly Reference.jpg
2020-09-23 Change resonator to part with interchangeable pins
    [BOM.xlsx, SinESC-Multi-2.3B.sch]
2020-09-24 Change total component count to correct value of 75, recalculate BOM Consolidation Ratio
    [BOM.xlsx]
2020-10-01 Add plain gerber files in addition to zipped gerber files
    [SinESC-Multi-2.3B-B_Cu.gbr, SinESC-Multi-2.3B-B_Mask.gbr, SinESC-Multi-2.3B-B_Paste.gbr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]
2020-10-09 Update solder paste settings for improved yield (when assembled with stencil)
    [SinESC-Multi-2.3B-B_Cu.gbr, SinESC-Multi-2.3B-B_Mask.gbr, SinESC-Multi-2.3B-B_Paste.gbr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]
2020-10-09 Temporarily remove Wing Edition files
    [1.0A Capacitors.xlsx, 1.0A Final BOM for Assembly.xlsx, 1.0A Final BOM.xlsx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]
2020-10-09 Add Wing Edition files
    [1.0A Capacitors.xlsx, 1.0A Final BOM for Assembly.xlsx, 1.0A Final BOM.xlsx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]
2020-10-09 Add Dev materials
2020-10-15 Update assembly references
2020-12-27 Rename all project files to stop reflecting board version
    [BOM.xlsx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]
2020-12-28 Fix issue in the schematic in which the buck converter's 3.3V output is not connected to the rest of the 3.3V rail
    [SinESC-Multi.sch]
2020-12-28 Implement critical fix according to updated schematic, several other small updates (layout & silkscreen conditioning)
    [SinESC-Multi.kicad_pcb]
2020-12-28 Modify all exported files to reflect PCB changes
    [BOM.xlsx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]
2020-12-29 Change via drill diameter to 0.2mm from 0.254mm. This allows the design to take full advantage of PCBWay's capabilities, while it remains compatible with OSH Park's minimum design rules as well (as t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
    [SinESC-Multi-B_Cu.gbr, SinESC-Multi-B_Mask.gbr, SinESC-Multi-B_Paste.gbr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]
2020-12-29 Remove gerber files. It is best to generate these manually when necessary.
    [SinESC-Multi-B_Cu.gbr, SinESC-Multi-B_Mask.gbr, SinESC-Multi-B_Paste.gbr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]
2020-12-30 Decrease STM32 LQFP48 pad size from 0.3mm to 0.28mm so more manufacturers support solder mask between the pads
    [SinESC-Multi.kicad_pcb]
2020-12-30 Update date reflected on sheet. Remove "Made in USA" from silkscreen to avoid customs issues when ordering boards from outside the U.S.
    [SinESC-Multi.kicad_pcb]
2020-12-30 Update "Source" field in BOM to reflect latest file name and path
    [BOM.xlsx]
2020-12-31 Fix another issue in which the bootstrap capacitors were not connected to the source pins of the high-side FETs
    [BOM.xlsx, SinESC-Multi.kicad_pcb, SinESC-Multi.sch]
2021-01-10 Ignore "fp-info-cache" KiCAD file
2021-01-18 Add packages/footprints to BOM
    [BOM.xlsx]
2021-01-22 Add several useful STM32 docs
2021-01-25 Multiple changes to SPI code and TMC6100 config
2021-06-30 Reorganized/moved old files, added additional red-only and black-only logos
    [1.0A Capacitors.xlsx, 1.0A Final BOM for Assembly.xlsx, 1.0A Final BOM.xlsx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]
2025-10-30 remove old stuff and add slides
    [1.0A Capacitors.xlsx, 1.0A Final BOM for Assembly.xlsx, 1.0A Final BOM.xlsx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]

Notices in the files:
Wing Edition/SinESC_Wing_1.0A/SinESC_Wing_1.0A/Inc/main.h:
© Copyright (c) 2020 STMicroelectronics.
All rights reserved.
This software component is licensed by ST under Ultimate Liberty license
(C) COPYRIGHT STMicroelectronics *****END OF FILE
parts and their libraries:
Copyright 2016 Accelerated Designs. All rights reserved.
